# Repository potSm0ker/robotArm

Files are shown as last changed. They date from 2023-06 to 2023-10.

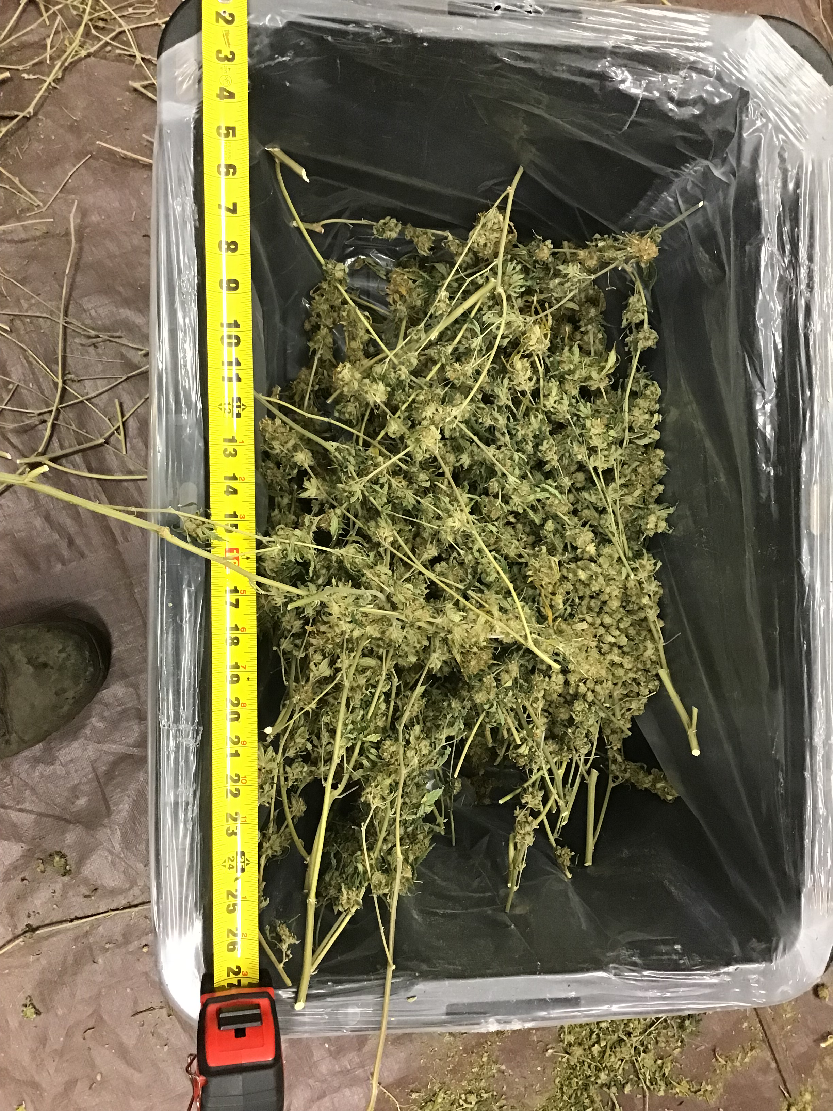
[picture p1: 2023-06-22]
workspaceExamples/binMeasured.jpg

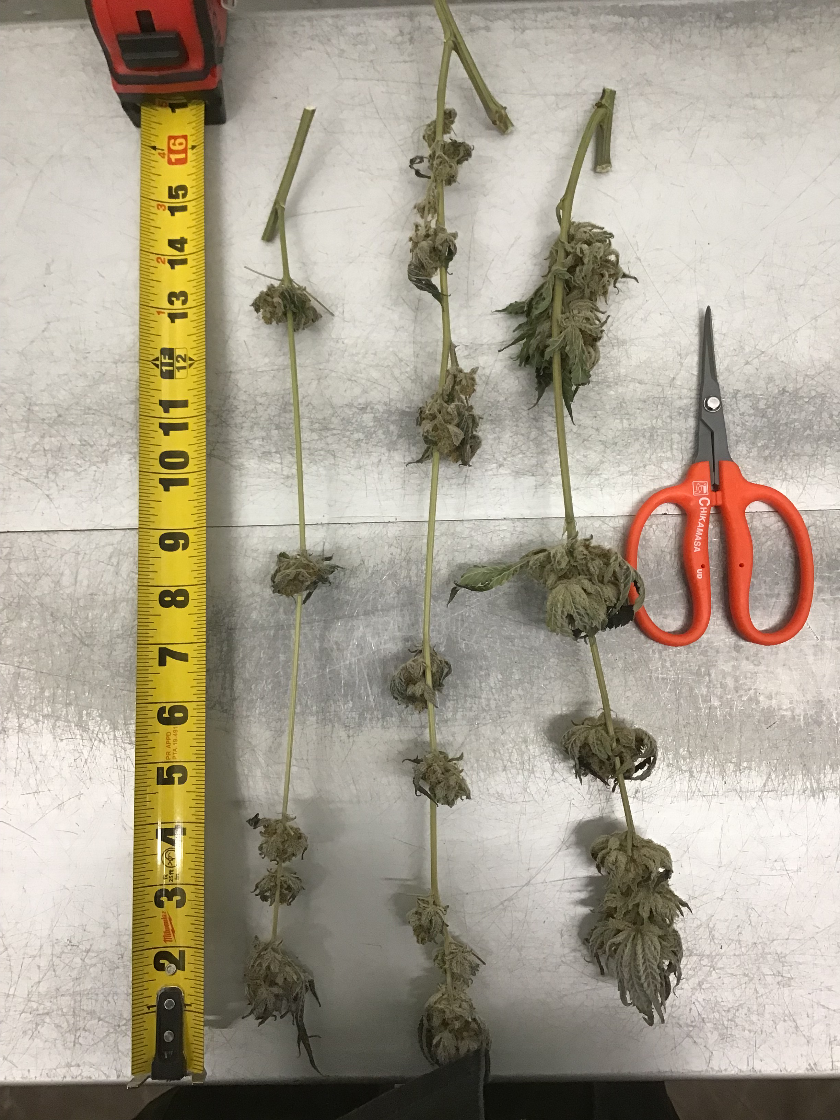
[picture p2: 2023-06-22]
workspaceExamples/branchMeasured.jpg

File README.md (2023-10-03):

# Trim Bot Project

<details>

<summary> ***30,000 foot goal.*** Create a pair of electric robot arms that can trim 1 pound of dried cannabis buds in 8 hours.  </summary>

- Create a pair of electric robotic arms that can **automatically** trim dried cannabis flowers using a standard pair of trimming scissors. **The target goal is to trim 1 pound of cannabis in 8 hours time.** The arm uses servo motors to rotate the joints. For vision- open cv or other methods of object detection using one or more cameras. The arm will be able to grasp (using a two fingered-claw) a branch or bud from a bin full of branches, then hold the branch while a second arm with standard trimming scissors attached (to the claw) will trim the buds. The finished buds will be dropped into a bucket when complete. The average human trimmer would trim for about 7.2 hours in a standard work day, 1 pound of trimmed cannabis would be the expected minimum after 8 hours. 2 pounds would be a high amount for a human trimmer in a standard 8 hour work day.
- I have a real world application for this robot. I can put it to work immediately after it is finished. I work in the cannabis industry, so I hope to have this finished before I lose my position here and have to move to a different industry. I have advanced as far as I can in the company I work for, so this is a way to advance my career without having to completely switch industries and have to start from the bottom.

<summary> ****The pair of robot arms should do the following:**** </summary>

- trim = remove all fan leaves using standard trimming [scissors](http://www.chikamasa.com/products/index.cgi?key=27) (see workspaceExamples directory) I will be using CHIKAMASA B-500SF shears(I refer to them as scissors)

- Able to grasp a branch or bud with pincer-type end effector(2 finger claw)

- Able to open and close a pair of standard trimming scissors, which will be securely attached to end effector(claw). Scissors will be detachable from claw for cleaning.

- Able to identify a single branch or bud in a bin full of similar items.

- Will need camera for object detection. 
    - using open-cv or other methods. python or c++ maybe used.
    - Yolo v5 is compatible with jetson nano.
- Able to work together as a pair of arms, one will hold the scissors(scissor arm), the other will hold a branch/bud(branch arm).

- Branch arm able to identify fan leaves on bud and coordinate with scissor arm to remove all fan leaves.

- Branch arm able to rotate the bud/branch while scissor arm opens and closes scissors to complete trim.

</details>

- I am using a RaspberryPi 4 attached to a robot arm purchased from [amazon.com](https://www.amazon.com/Yahboom-Controlled-Programmable-Robotics-Identity/dp/B09T96PS3S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)
- For a complete 3d printable robot arm, [Moveo BCN3D](https://github.com/BCN3D/BCN3D-Moveo) I may adapt the design for my uses
- Also check out this repository [Robot Arm 3d printable](https://github.com/AngelLM/Thor/tree/developer)
- I would use a 3d printing service such as www.xometry.com to print parts.
<details>

</details>

- Here is a link  to a [YouTube playlist- Build a Robot Arm](https://www.youtube.com/playlist?list=PLcbaYozXcpF65uUvdCmepFYYjx4FZ4Iwq), these videos have info that may assist in completing the goal.
I will store the info I find useful in this repository. Some code maybe generated by chat-gpt or similar methods.

### See [workspaceExamples](https://github.com/potSm0ker/robotArm/tree/main/workspaceExamples) folder for visual definition of bud, branch, fan leaf and other items.

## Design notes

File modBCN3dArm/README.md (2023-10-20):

Blender file contains modified parts, from the BNC3d robot arm Github repository.  I set it up so i could test the range of the arm and see how it interacts with working environment. 
Created with blender 3.4

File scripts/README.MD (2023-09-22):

These are scripts that I am using to control the robot and help me complete my goal of creating a pair of autonomous cannabis trimming robot arms.
Some of these scripts may only work on a raspberry pi. In the jetson nano scripts folder are scripts that were developed for jetson nano and yahboom expansion board. I started this project with the jetson nano and expansion board but switched to raspberry pi 4 because it is more user friendly and has a larger community that can provide more answers to questions.

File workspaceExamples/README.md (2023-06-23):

## This folder contains images of products the robot arm will handle and environment the robot will traverse
### The physical working environment and equipment will be described here

<details>

<summary> Definitions </summary>

### These are items that will be used in the day to day operations involving the robot.

- buds = also called flower or nugs, the final product that will be sold to consumers, the end goal
- fan leaves = attached to the buds, they will be removed with scissors and collected for processing and sale
- branches = buds are attached to the branches. The branches will be discarded after the buds are trimmed
- bin = a black plastic container used to store branches and bud. Some buds may not be attached to branches
- scissors =  standard trimming scissors will be used, available locally and normally used by human trimmers
- tray = a black plastic tray used for collecting fan leaves and trimmed buds
- bucket = a white 5 gallon plastic container that will be used to store the finished buds

</details>

## The obective is to remove the fan leaves from the buds using scissors

- Branches may be in the range of 2 inches to 24 inches length.
- Buds(flower) may be in the range of .1 inch to 3 inches in length.
- The bin dimensions are  H- 15.27 inches, W- 19.61 inches, D- 28.55 inches
- The 5 gallon bucket dimensions are H- 15 inches, D- 10 inches
- The tray dimensions are H- 5 inches, W- 18 inches, D- 10 inches
- The working space for a normal human trimmer is approximately H- 4 feet x W- 3 feet x D- 3 feet

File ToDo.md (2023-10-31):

- i want to recreate the motion of two human arms, one connected to a pair of scissors, the other holding a branch/bud while the scissor arm trims the leaves from the bud
******* 

- i obtained a 3d printer and will print a modified version of bnc3d moveo robot arm
- i will redesign the scissor arm to use a nema 17 stepper motor to open and close the scissors, this should provide sufficient torque and precision. 

- The tip of the scissor gap must have sufficient torque to cut the branch and seperate the bud from branch
- physical trim test performed with 55kg servo, leaves can be trimmed, however the tip of the scissors are not getting enough torque to cut through the branch at the branch/bud intersection.
- may need to redesign end effector
- yolov8 segmentation? combined with oak d multiple nn detections
- how to identify and return position of leaves that need to be trimmed
- range for oak d camera- Ideal range: 70cm - 8m, MinZ: ~20cm (400P, extended), ~35cm (400P OR 800P, extended), ~70cm (800P)
- i attached camera to an extension rod and steel flat bar(14 inches), it is approximately 18 in from scissors, in a fixed location behind the scissors
- for best results using spatial detection, the camera should be perpendicular with scissors, the spatial detection fails with distance of less than 11 inches  
- using custom yolov5s model and Oak D camera, i created a script that would open and close scissors when a bud is detected within 600mm(z coord) of the camera.  

https://colab.research.google.com/github/luxonis/depthai-ml-training/blob/master/colab-notebooks/YoloV5_training.ipynb

- [Make Sense AI](https://www.makesense.ai/)    -browser based, no download, no install

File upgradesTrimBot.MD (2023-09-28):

To make the robot arm (with raspberry pi 4) do what I need to do, it will need some upgrades. 

# Current parts list

### Raspberry Pi 4 with geeekpi ice tower cooling fan and servo hat
 - using [raspberry pi 4](https://www.raspberrypi.com/products/raspberry-pi-4-model-b/) for computing and to control servos
 - pwm  16 servo hat from adafruit
 - geekpi ice tower cooling fan

### Vision - Oak-D pro camera(manual focus) from [Luxonis](https://shop.luxonis.com/products/oak-d-pro)
 - detection model can run on camera, inference results will be sent to nano
 - will use yolov5 custom model to identify leaves and direct scissors to trim leaves
 - yolov5 for locating and picking branches from bin
 - created custom bracket in blender to mount camera to robot
 - custom bracket 3d printed on [Xometry.com](https://www.xometry.com/)

# August 2023 - no longer using the parts below

### Jetson nano developer kit attached to yahboom expansion board
 - started with a jetson nano, the expansion board it was attached to had no documentation that I could find, so I switched to a raspberry pi 4 with gb ram and pwm servo hat to drive the servos.

### Increase storage  SAMSUNG T7 Portable SSD 500GB
 - I used win32disk imager to write the custom jetson image provided by yahboom for the robot arm
 - running operations on the jetson nano is much faster using an external ssd via usb3 rather than a micro usb drive.
 - run  gparted    in the terminal to see partitions and expand the file system partion to use the entire 500 gb SSD, in my case it was /dev/sda1 
 - boot from usb [jetsonhacks.com](https://jetsonhacks.com/2021/03/10/jetson-nano-boot-from-usb/)
 - create backups of critical files before attempting, loss of data may occur when trying to remount file system

### Upgrade cooling fan and heat sink - GeeekPi 5V PWM Low-Profile CPU Cooler
 - I upgraded to [Ice tower cooling fan](https://www.amazon.com/GeeekPi-Low-Profile-Horizontal-Radiator-Colorful/dp/B07ZYW6ZVR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) from amazon.com

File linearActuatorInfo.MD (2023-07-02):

## info is specific to this particular project, maybe used for other projects
- Needed for this project- slide rail(linear actuator lead screw) with a length of at least, 1000mm (3 feet), to increase reach of the robotic arm
- will be mounted vertically on a wall, with robot arm attached to slide rail on a plate.
-  lead screw-driven actuators with slide rail
- nema23 stepper motor connect to jetson nano
- Digital Stepper Driver 1.0-4.5A 18-50VDC for Nema 17, 23, 24 Stepper Motor $17.88
- for connection  USB to TTL Serial Cable or FTDI Serial TTL-232 USB Cable

 - Connect the motor driver to the Jetson Nano: usb to ttl cable. The motor driver will typically use digital input pins to receive control signals from the Jetson Nano. 

- websites
 - https://openbuildspartstore.com/
 - [How to Implement a Linear Stage With Raspberry Pi](https://www.digikey.com/en/articles/easy-build-how-to-implement-linear-stage-raspberry-pi-project)

### commercially available slide rails some assembly required

- [how to assemble slide rail from open build part store](https://www.youtube.com/watch?v=56RIplHaoQs&list=PLDeI80MYQtbqZahZvCIcOPhE0wO3RirvY)
- [OpenBuilds C-Beam Linear Actuator Lead Screw 1500mm](https://openbuildspartstore.com/c-beam-tension-xl-linear-actuator-bundle/) $261.97
- [nema 23 motor + controller with usb to ttl](https://excitron.com/secure/?itemid=585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) $279.00 

- ## stepper motor drivers
- www.teknic.com
- [top choice - clear path motors](https://teknic.com/products/clearpath-brushless-dc-servo-motors/clearpath-sc/)
- [clear path motors youtube](https://www.youtube.com/watch?v=1S7etlhbuFY&list=PLuMmdjFz-3nzWAxdQWN__v9P9fYJkGCvS&index=2)
- [connect clear path motor  to arduino](https://www.youtube.com/watch?v=QZLwDnGSaeI&list=PLuMmdjFz-3nzWAxdQWN__v9P9fYJkGCvS&index=8)

 - [RTELLIGENT Nema 23 Stepper Closed Loop Servo Motor and Driver Kit 2 Phase 3.0NM(425 oz.in) with Encoder](https://www.amazon.com/RTELLIGENT-Stepper-Closed-57X57X119mm-Encoder/dp/B07ZLQL83N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)

 - [CNC Digital Microstep driver DM542 Stepper Motor Controller 2-phase Digital Stepper Motor Driver 20-50V DC Max 4.2A](https://www.amazon.com/Digital-Microstep-Stepper-Controller-2-phase/dp/B08GCFNQF2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)

 - [STEPPERONLINE 1 Axis CNC Kit 3Nm(425oz.in) Nema 23 Stepper Motor & Driver](https://www.amazon.com/STEPPERONLINE-425oz-Stepper-Driver-Router/dp/B012QFRKAO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)

## power supply
- [DROK 36V Power Supply, AC 110V 220V to DC 0-36V 4A 150W Buck Converter](https://www.amazon.com/DROK-110V-220V-Converter-Adjustable-Transformer/dp/B0B18P6GKP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)

### Found diy video and parts list

[DIY slide rail assembly youtube](https://www.youtube.com/watch?v=bwkWi0-p5mU)
- parts list for a DIY linear rail
 - Aluminium profile T-Slot 30cm
 - Aluminium profile T-Slot 5cm
 - Linear guide rail MGN12H 30cm
 - T8 2mm pitch lead screw 30cm & anti backlash nut
 - NEMA 17HS8401 stepper motor
 - NEMA 17 fixed mount bracket
 - 5-8mm flexible coupler
 - M3 Female2male brass screw thread PCB stand
 - M5 hex screw + nut + flat washer
 - M3 hex screw + nut
 - Zip ties

 [mini jetson nano car](https://medium.com/@anandmohan_8991/jetbot-using-l298n-pwm-motor-a6556ed358d6)

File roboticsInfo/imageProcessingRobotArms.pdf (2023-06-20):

See discussions, stats, and author profiles for this publication at: https://www.researchgate.net/publication/261225894
Practical applications for robotic arms using image processing (https://www.researchgate.net/publication/261225894_Practical_applications_for_robotic_arms_using_image_processing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)

Conference Paper · January 2012

CITATIONS
17

READS
9,894

### 3 authors, including:

Some of the authors of this publication are also working on these related projects:

Nonlinear Fault Tolerant Control for Real-Time Robotics View project (https://www.researchgate.net/project/Nonlinear-Fault-Tolerant-Control-for-Real-Time-Robotics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)

Intelligent control structure and navigation system based on the performance sensors, video-biometric and video-servoing sys. for complex autonomous sys. CAS-IW integrated into the technology for assisting people with severe neuro motor disabilities View project (https://www.researchgate.net/project/Intelligent-control-structure-and-navigation-system-based-on-the-performance-sensors-video-biometric-and-video-servoing-s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)

R. Solea (https://www.researchgate.net/profile/R-Solea?el=1_x_5&_esc=publicationCoverPdf)
Universitatea Dunarea de Jos Galati (https://www.researchgate.net/institution/Universitatea_Dunarea_de_Jos_Galati?el=1_x_6&_esc=publicationCoverPdf)

### 70 PUBLICATIONS 482 CITATIONS

SEE PROFILE (https://www.researchgate.net/profile/R-Solea?el=1_x_7&_esc=publicationCoverPdf)

All content following this page was uploaded by R. Solea (https://www.researchgate.net/profile/R-Solea?el=1_x_10&_esc=publicationCoverPdf) on 08 December 2014.

The user has requested enhancement of the downloaded file.

## Practical Applications for Robotic Arms Using Image Processing

Mihai Dragusu¹

, Anca Nicoleta Mihalache¹

and Razvan Solea²
, member, IEEE

Abstract— The following paper presents various applications for a robotic arm using image processing. These applications have as a basis a video camera that captures the images to be processed for either recognition and sorting or for contour coordinates extraction. Based on these captures, there were developed algorithms that enable the arm to either sort objects recognized to be having different shapes, or to draw shapes based on the coordinates received. Both the object detection and the contour coordinates extraction methods are implemented using a series of image processing techniques like border extraction, contour detection, contour extraction, along with match template and the aid of OpenCV library. Also, a PI controller that ensures the position of the robotic arm was developed.

I. INTRODUCTION
The influence and impact of digital images on modern society, science, technology and art are huge. Image processing has become such a critical component in contemporary science and technology that many tasks would not be attempted without it. It is a truly interdisciplinary subject and is used in computer vision, robotics, medical imaging, microscopy, astronomy, geology and many other fields [1] - [5].
One of the core technologies of the intelligent robot was, of course, vision, and this vision research area was called ”computer vision”, which is now regarded as a fundamental and scientific approach to investigate how artificial vision can be best achieved and what principles underlie it [6]. OpenCV (Open Source Computer Vision) is a library of programming functions for real time computer vision. OpenCV is free for both academic and commercial use. It has C++, C, Python and soon Java interfaces running on Windows, Linux, Android and Mac. The library has more then 2500 optimized algorithms [7].
OpenCV played a role in the growth of computer vision by enabling thousands of people to do more productive work in vision. With its focus on real-time vision, OpenCV helps students and professionals efficiently implement projects. The contribution of this paper is to report new practical applications for student laboratory that provide the hands-on experience that is critical for robotics education. These types of exercises supply the student with hands-on experience that complements classroom lectures and software development. Through this experience, the student confronts the hard realities of robot systems; realities such as sensor noise,

1M. Dragusu and A.N. Mihalache are students at the Faculty of Automatic Control, Computers, Electric and Electronic Engineering, “Dunarea de Jos” University of Galati, Romania dragusumihai@yahoo.com, mihalache anca@ymail.com
2R. Solea is with the Faculty of Automatic Control, Computers, Electric and Electronic Engineering, “Dunarea de Jos” University of Galati, Romania razvan.solea@ugal.ro

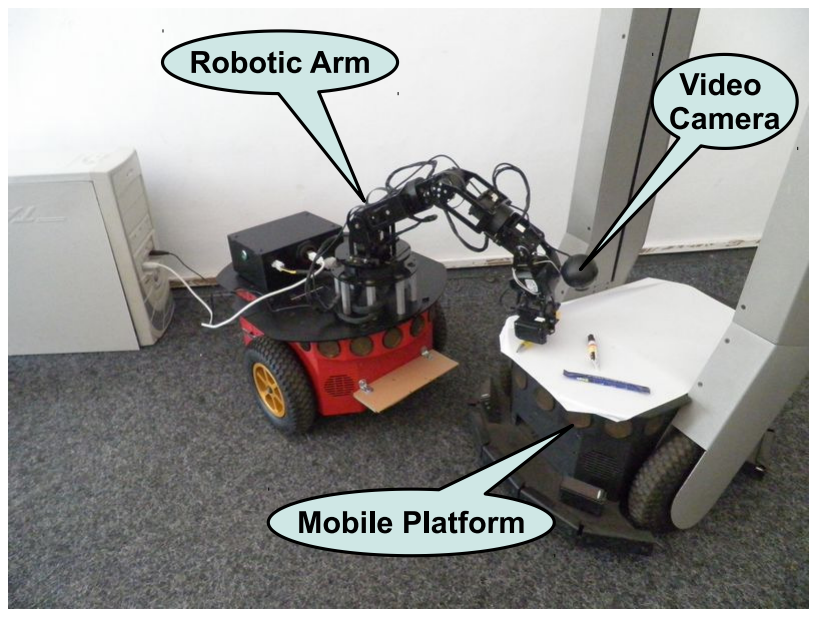
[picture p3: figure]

Fig. 1. System hardware components

nonzero calibration residuals, low fidelity of models, and real-time constraints; and learns to deal with them.
The goal of this paper is to provide an overview of the practical laboratory applications and the required facilities. As an overview, the paper will provide enough practical information to replicate the applications.

II. PRACTICAL APPLICATIONS - ALGORITHMS

The system is designed for processing images captured by a web cam so important information can be extracted and sent to the robotic arm. The robotic arm has a software implemented, so it can use the information received in order to complete its given task: either recognize shapes for sorting or coordinates extraction from a contour for drawing. System hardware components are (see Fig. 1): video camera and processing tool, robotic arm and mobile platform.

A. Contour Coordinates Extraction

The web cam captures the image to be processed. In order to obtain information about this capture, edge detection applied to the image is necessary.
Of all the edge detection techniques (Canny, Sobel, Laplace, etc.), Canny method [10], [11] was chosen because of its good performances with noisy images. This algorithm can only be applied on a grayscale blurred image, and it will find all the edges from the image, based on which contours will be formed.
After using Canny algorithm on the blurred image, it has been decided that each contour would have associated a different shade of red for each limited entity, starting from 254 and decrementing this value in successive steps with 1 until reaches the value 10. This means the detection and distinguishing of up to 244 discontinuous contours. But in

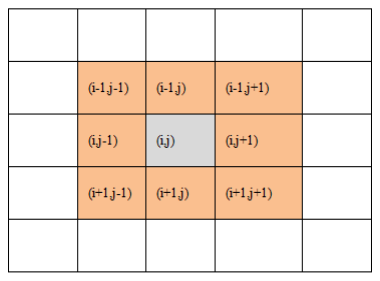
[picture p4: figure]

Fig. 2. The Moore neighborhood in coordinates

the captured image there can also exist continuous contours, that can be detected as such, and be assigned another color (blue).
These operations result in an image that contains all boundaries (edges) found in the web cam capture. These contours will have their coordinates extracted in order to be sent to the robotic arm.
It has been chosen the design of an algorithm that is optimal for the issue at hand, the drawing with the robotic arm. The image to be processed is analyzed as a matrix, and the coordinates (x, y) of a given color are saved in a matrix of unsorted coordinates.
For the drawing to be facilitated for the robotic arm, it is of the essence that the drawing of a contour does not start from a random point that first found by the algorithm, but from a start pixel of that contour (a pixel that only has one neighbor in the Moore neighborhood - see Fig. 2).
Once the start pixel is found, based on its coordinates, the sorting of addresses from the unsorted coordinate matrix will follow. This sorting is based on applying an optimization criterion that ensures finding the neighbor of the current pixel. This criterion is represented by the distance between the pixel considered current pixel, and the pixel analyzed from the unsorted addresses matrix. The sorting of the addresses is made based on this criterion, and the update of the current pixel is made by assigning the last pixel to be sorted at any point in the algorithm as the current pixel for the next iteration.
Once the address of a pixel is sorted, its coordinates are to be erased from the initial matrix, and added in the sorted coordinates matrix. This is easily followed in the following code:

if (dist < min_dist) //if current distance is lower that the minimum distance {
min_dist=dist; | //current distance is
| minimum distance
poz_adr=i;
adr_ord[linie][0]=adr1[i][0]; adr_ord[linie][1]=adr1[i][1]; }
else
{
if(dist==min_dist)
{

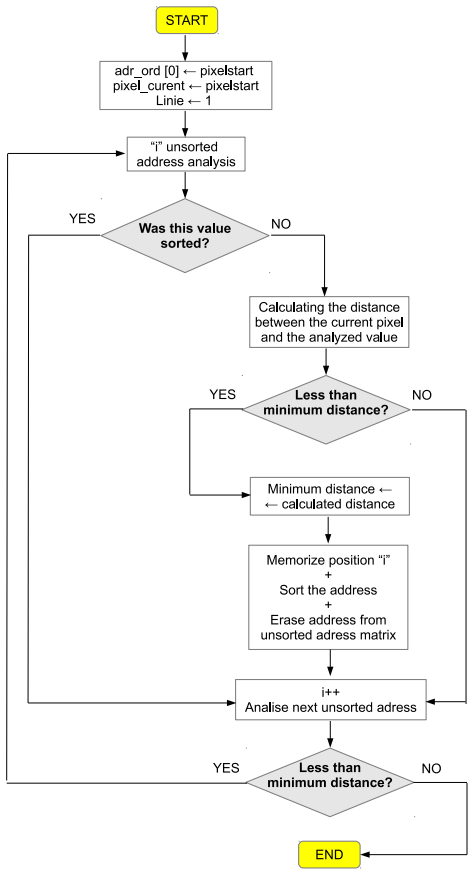
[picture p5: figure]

Fig. 3. The sorting algorithm

adr_ord[linie][0]=adr1[i][0]; adr_ord[linie][1]=adr1[i][1]; }
}
adr1[poz_adr][0]=-1;
adr1[poz_adr][1]=-1;
pixel_curent[0]=adr_ord[linie][0]; pixel_curent[1]=adr_ord[linie][1]; linie++;

The sorting of contour coordinates algorithm is presented in Fig. 3.
This implementation prevents the double passing on the same contour/region. So with this solution, no coordinate once sorted would be ever checked again. This is a very important aspect, considering the task given, because drawing the same piece of contour several time is not only useless for the arm, but also it can also emphasis the hardware limitations of the system-drawing the same piece of contour will not overlap on several drawings, even if the given coordinates are the same ones. This event occurs because of the hardware parts involved, like the arm′
s encoders.
B. Robotic Arm Software for Sorting Algorithm
In order to obtain information about the presented object, edge detection applied to the image is necessary. For the

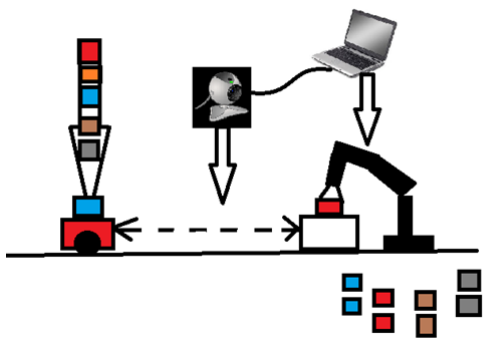
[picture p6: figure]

Fig. 4. Object recognition and sorting solution

same reason, Canny method was again chosen. After the edges are extracted from an image a contour (chain of neighbor pixels) finding method can be applied. Some contours may contain the object, since the edge of one object is a chain of pixels.
The actual recognition is realized with match-template method, which consist in placing a frame containing the object on top of the current image, calculating the sum squared error and then moving the object through the image in order to determine where the sum squared error is minimal.
It can be easily observed that the method above can prove inefficient if the number of objects to be found increases, or the size of the image increases. The application will end up looking for a 50 × 50 image in a 1920 × 1080 image filled with irrelevant data except for the actual object.
So in order to increase efficiency another method was designed based on match-template. This new method will use edge detection, contour detection, and contour extraction on the current image and only then will match-template be used between the searched object and the object extracted from the current image (resized to the dimension of the searched object). This way the application will use match-template only on relevant data, not blindly on the entire image.
For object sorting algorithm (see Fig. 4), the robotic arm will go through four states:
- A initial position at which the robotic arm will go once the control application is launched. From this position the camera placed on the arm will capture the image containing the object in order to determine its category.
- A state in which the gripper is brought to the object’s level in order to grab it.
- Return to the initial position, but this time with the object grabbed (this state is an intermediate state to avoid collision with the mobile platform if the arm were to go directly to the last state)
- The last state is actually a multitude of states generated by the object’s category (each category has assigned a different location)
The object recognition and sorting algorithm is presented in Fig. 5, where: Xdorit is the position where the mobile

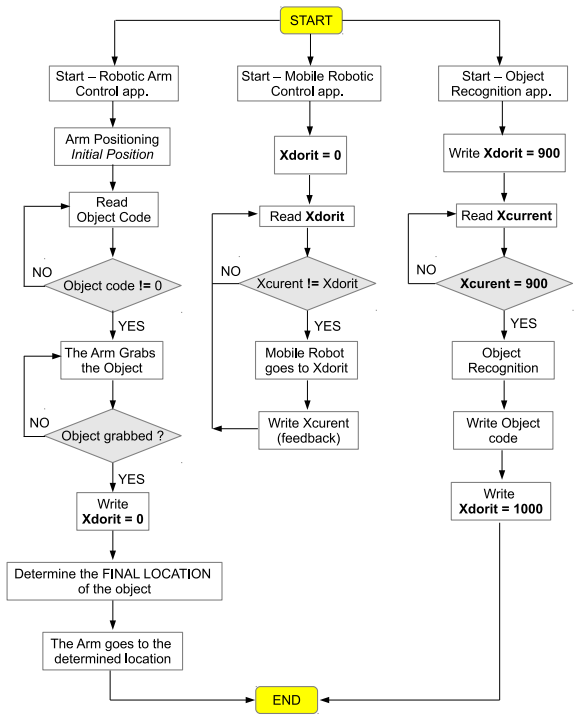
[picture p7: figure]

Fig. 5. Object recognition and sorting algorithm

Fig. 6. The control structure of robotic arm

platform should be (0 initial postion, 900 [mm] in front of the camera to determine the object, 1000 [mm] in front of the robotic arm so that it can grab the object); Xcurent is the feedback given by the platform; ObjectCode is an number which represents the detected object (the algorithm uses this number to determine the depositing position).
The control software (actinSE) [9] implemented for this robotic arm has a controller designed, but this controller does not offer the precision needed for this project so a P I controller (see Fig. 6) was designed to correct the command given by the actinSE controller.

III. FIRST PRACTICAL LABORATORY APPLICATION - EXPERIMENTAL RESULTS FOR IMAGE DRAWING

A. Step 1 - Image capture and processing

The web cam included in the system makes an image capture to be processed. Firstly it is needed to set a blur and a Canny threshold according to the image, environment and noise of the camera, with the help of this user-friendly interface, Fig. 7.

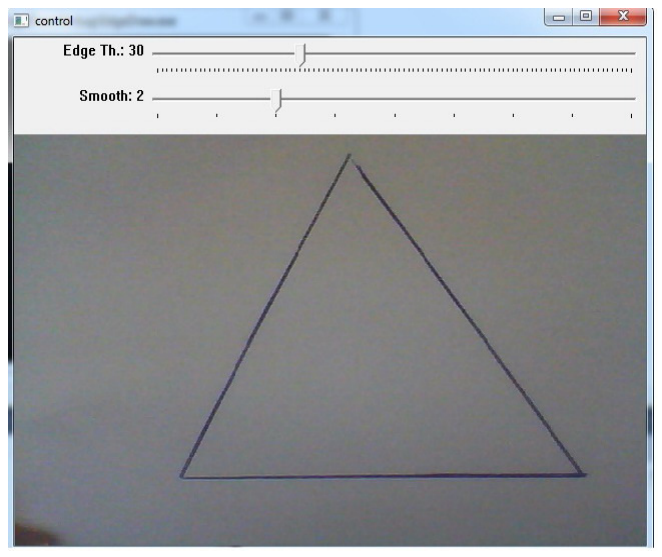
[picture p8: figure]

Fig. 7. Capture of the image to be drawn

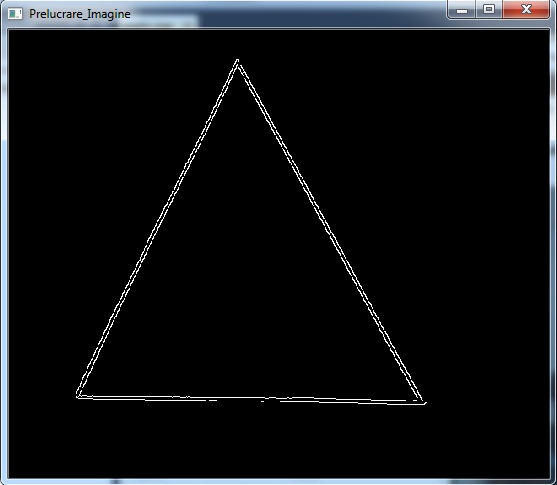
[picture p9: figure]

Fig. 8. The result of Canny algorithm on the captured image

The following code sequence is a demonstration on how the capture is prepared for Canny algorithm, by transforming it in a blurred single-channel image:

frame = cvQueryFrame( cv_cap); cvSmooth(frame,frame,CV_GAUSSIAN,smoothD,smoothD); IplImage* frgray = cvCreateImage( cvGetSize(frame), IPL_DEPTH_8U, 1 );///frame in grayscale cvCvtColor(frame, frgray, CV_RGB2GRAY );
The result of applying Canny algorithm is presented in Fig. 7, obtained with the following code sequence:

cvNamedWindow("Prelucrare_Imagine",0);
frame = cvQueryFrame( cv_cap);
cvSmooth( frame, frame,CV_GAUSSIAN,smoothD, smoothD);
cont=Canny(frame);
cvShowImage("Prelucrare_Imagine", cont);

As mentioned, these contours are to be colored in red for an easier analysis.

B. Step 2 - Robotic arm drawing coordintes
The coordinates that were extracted from this image are the Cartesian coordinates to be rescaled and translated in polar system. But for demonstration purposes, these coordinates were used for a Matlab simulation, where it was created a matrix of addresses to be plotted:

for i=1:1:s(2)
plot(a(1,i),a(2,s(2)-i));
hold on
pause(0.001);
axis([0 640 0 640]);
end

And the image that results is drawn fluently point by point for an easier observation on where the contour starts and how the contour drawing is progressing, as if the arm would be drawing. The final result of the Matlab simulation is described in the Fig. 9.
Robot arms offer significant advantages for robotic tasks. With many degrees of freedom, they are able to reach around obstacles, reconfigure for strength, improve accuracy, and manipulate objects with dexterous fluid motion.
Combined with Energid’s 3D visualization, reasoning, and control software, the Cyton V2 manipulator [8] can perform advanced control by exploiting kinematic redundancy. Cyton have 7 DOF plus gripper, all axes are completely independent yet can be controlled simultaneously (using the included Actin control software). Also, it has high performance, intelligent actuators give feedback on position, speed, load, voltage, and temperature.

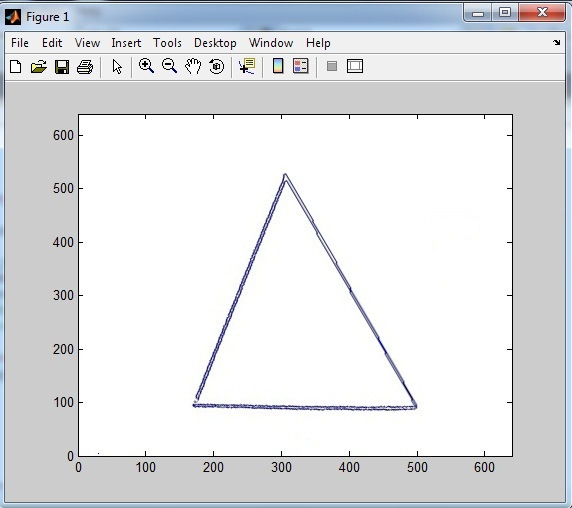
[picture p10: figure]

Fig. 9. Matlab simulation of drawing the extracted coordinates

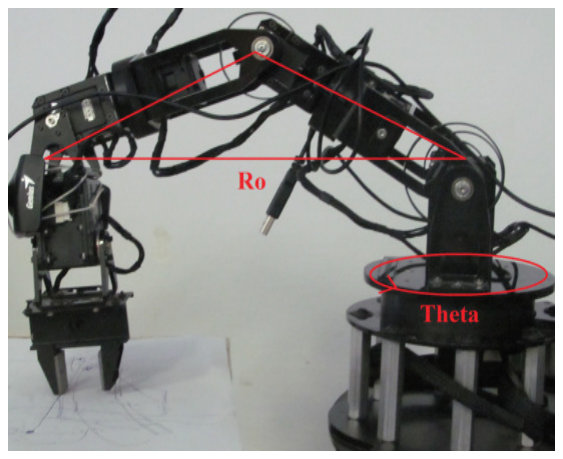
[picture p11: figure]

Fig. 10. Polar coordinates defined on the robotic arm

As for the drawing algorithm, as it was mentioned before, the coordinates provided by the contour extraction algorithm are in Cartesian system, so for the actual drawing process, they need to be converted to polar coordinate system.
The real space in which the arm can draw is limited because the distance it can reach (ρ) is not scaled correctly related to its angle (θ) (see Fig. 10. In order to solve this problem, a new scaled space had to be defined like in Fig. 11.
The polar coordinated for this space (P) were experimentally determined, and then transformed back into Cartesian coordinates (C).

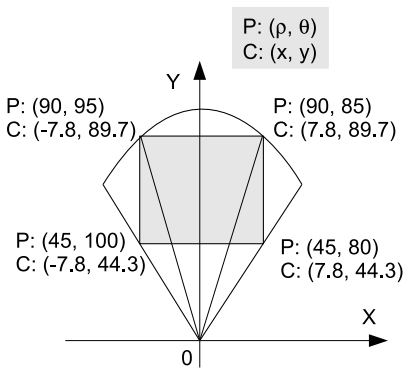
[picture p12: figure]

Fig. 11. The scaled space defined in polar coordinates

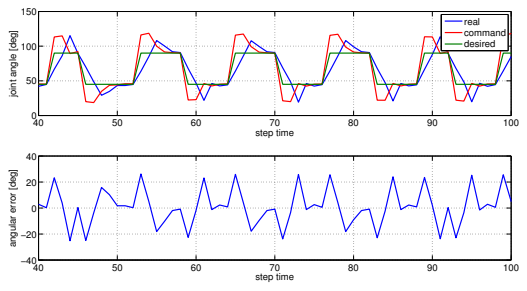
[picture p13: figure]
step time; angular error [deg]; joint angle [deg]; real command desired

Fig. 12. Joint angle variation

Knowing that the image has a width of 640 pixels and a height of 480 pixels, and based on the C coordinates calculated, two constants, one for each axis, needed to be determined, so that the coordinates extracted from the image can be scaled to this newly defined space:
- x axis rescale K1 = 15.6/640 = 0.024, where 15.6 = 2 ∗ 7.8 the distance between −7.8 and 7.8;
- y axis rescale: K2 = 45.4/480 = 0.094, where 45.4 = 89.7−44.3, roughly the distance between 89.7 and 44.3. Once these constants have been defined, the rescale formula for the Cartesian coordinates is:

xr = x ∗ K1 − 7.8
yr = y ∗ K2 + 44.3

(1)

where xr | and yr | are the rescaled coordinates and x, y are
the initial coordinates provided by the extraction algorithm. So after rescaling the drawing space and the coordinates received from the extraction algorithm and transformed into polar coordinate system, the arm can now draw the shapes presented to the camera, with a low degree of difficulty, considering the limitations it has.
Fig. 12 shows the desired, command and real angular position of the first joint of the manipulator and the angular error.

IV. SECOND PRACTICAL LABORATORY APPLICATION - EXPERIMENTAL RESULTS FOR SORTING ALGORITHM
A. Step 1 - Learning Process (object extraction)
During this process the user will help the application learn which objects to detect, using the following steps: i) the image is captured (Fig. 13 and the edge detection is applied (“c” button); ii) the contours are determined (“d” button); iii) the objects captured by the contours are browsed (“n” button) until the user finds the desired object (see Fig. 15) and saves it (“s” button).
B. Step 2 - Recognition principle
During this process (see the diagram: Fig. 17) the camera feedback is constantly checked to see the same object extraction is applied for each frame only now for each object extracted match template is applied for each object saved. When the sum squared error between two objects is less than

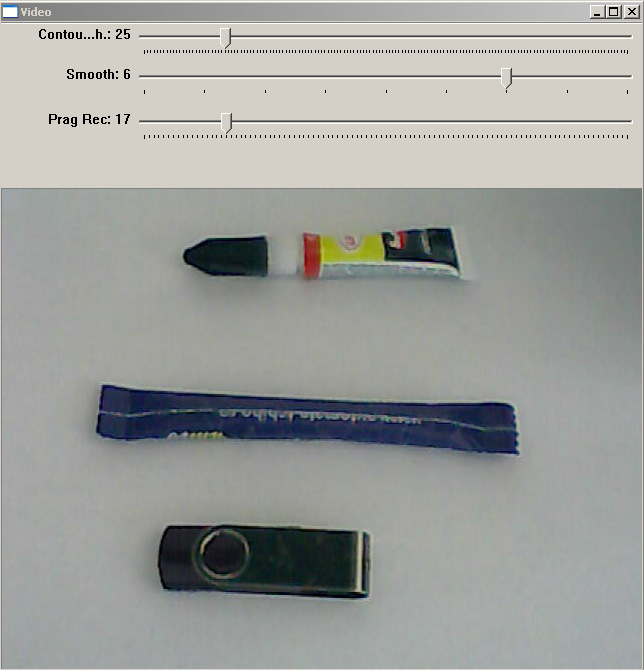
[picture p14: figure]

Fig. 13. Captured image

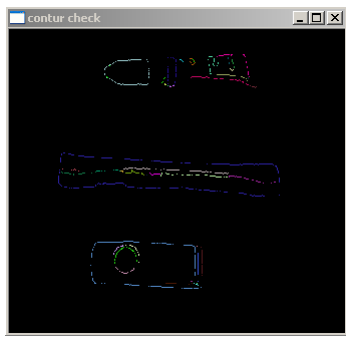
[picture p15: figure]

Fig. 14. Canny result

a predetermined threshold then we can say that the object we found (see Fig. 16 is the one were looking for.
The described process can find multiple objects in a single image.
In the following example the searched object is an USB flash stick.
In Fig. 18 the found object is declared (“stick.jpg gasit”) and its sum squared error compared to the saved one (0.0736217), as you can see other saved objects have been compared with the found object in the current image but none had the sum squared error (0.284048 and 1) low enough for a mismatch.
C. Step 3 - Object depositing

After the object has been found it’s assigned a code that is communicated to the arm’s control software which has specified places for each object type to be deposited.
To show the effectiveness of the proposed algorithm, experiments was made using a Pionner Robot mobile platform (like in Fig. 1). The mobile platform will pass through three states: i) Positioning at the input buffer coordinates; ii) Positioning under the camera in order to determine the

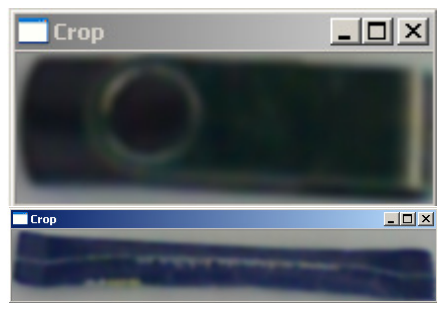
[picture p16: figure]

Fig. 15. Saved objects - example

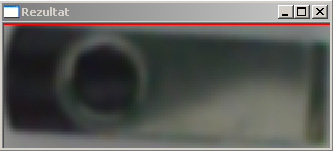
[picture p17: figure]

Fig. 16. Showing the found object

object, and to grab the object with the robotic arm; iii) Return to the initial position.
All three states are communicated (in form of Cartesian coordinates) to the mobile platform using ARIA (Advanced Robot Interface for Applications) software. The main application will write the desired position for the platform and the control application of the platform will read the file and command the robot to go to that position. ARIA software can be used to control the mobile robots like Pionner, PatrolBot, PeopleBot, Seekur etc. ARIA it is an objectoriented Applications Programming Interface (API), written in C++ and intended for the creation of intelligent high-level client-side software. ARIA provides tools to integrate I/O and includes comprehensive support for all MobileRobots robot accessories, including the laserrange finders, control of the pan-tilt-zoom camera or pantilt unit, Pioneer Gripper and Arm, and more.
V. CONCLUSIONS
In this paper it was presented practical laboratory applications in robotic manpulation, computer vision, and mechatronics. This applications provide the hands-on experience that is essential for robotics education.
The integration of real-world problems with complex imagery can improve image-processing applications. Effective applications-based exercises should be closely aligned with lecture concepts and should be assigned with little time delay. An “OpenCV” environment allows a focus on the imaging concepts and techniques with minimal programming difficulty.
Both applications, the object detection and the contour coordinates extraction methods are implemented using a series of image processing techniques like border extraction, contour detection, contour extraction, along with match template and the aid of OpenCV library.
In future work, motivated by this work, we consider the situation when mobile manipulators are sorting objects and placed the objects in a known location.

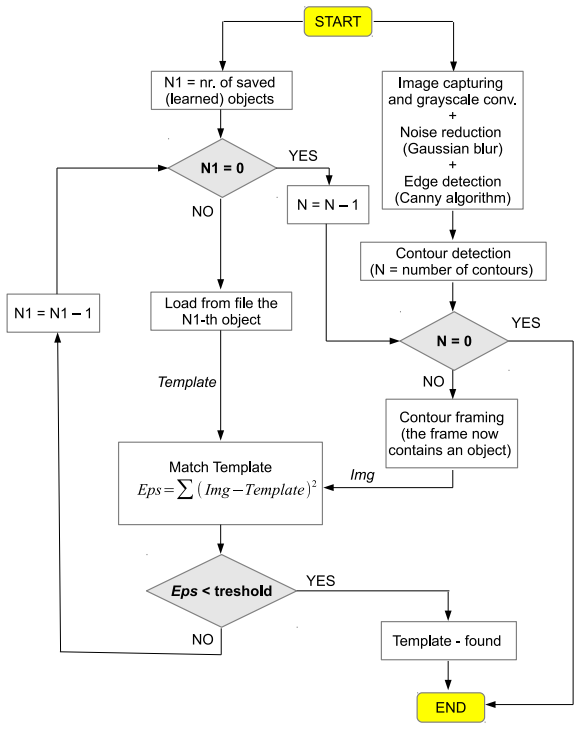
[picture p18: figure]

Fig. 17. The object recognition algorithm

Fig. 18. Result of recognition algorithm

REFERENCES

[1] C. Theis, I. Iossifidis and A. Steinhage, Image Processing Methods for Interactive Robot Control, Proceedings 10th IEEE International Workshop on Robot and Human Interactive Communication, 2001, pp. 424-429.
[2] G. Dougherty, Digital Image Processing for Medical Applications, Cambridge University Press, 2009.
[3] M. Pesenson, W. Roby and B. McCollum, Multiscale Astronomical Image Processing Based on Nonlinear Partial Differential Equations, The Astrophysical Journal, 683 (1), 2008, pp. 566-576.
[4] S. A. Drury, Image Interpretation In Geology, Nelson Thornes, UK, 2001.
[5] Yu-fai Fung, H. Lee, and M. F. Ercan, Image Processing Application in Toll Collection, IAENG International Journal of Computer Science, 32(4), 2006, 6 pages.
[6] M. Ejiri, T. Miyatake, H. Sako, A. Nagasaka and S. Nagaya, Evolution of Real-time Image Processing in Practical Applications, IAPR Workshop on Machine Vision Applications, Japan, 2000, pp. 177-186.
[7] G. Bradski and A. Kaehler Learning OpenCV (Book style), O’Reilly Media, Inc., USA, 2008.
[8] Robai, CYTON V2 7DOF - Operating Manual, USA, 2010, 36 pages.
[9] Energid Technologies, Energid ActinSE Documentation,
http: //www.robai.com/content/docs/ActinSE docs/.
[10] R. C. Gonzalez and R. E. Woods, Digital Image Processing, 3rd Edition, Prentice Hall, 2008.
[11] W. K. Pratt, Digital Image Processing: PIKS Inside, 3rd Edition, John Wiley & Sons, Inc., 2001.

View publication stats (https://www.researchgate.net/publication/261225894)

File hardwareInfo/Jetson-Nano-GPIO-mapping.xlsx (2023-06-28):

Jetson Nano J41 GPIO Expansion Header Mapping (derived from Jetson.GPIO data)
Connector Pin # | RPi Connector Label | RPi Default SoC Pull | Module connector signal name | Linux GPIO Within Chip | Assumed Linux GPIO Chip Base | Linux GPIO
1 | 3V3
2 | 5V0
3 | SDA1 | High
4 | 5V0
5 | SCL1 | High
6 | GND
7 | GPIO_GCLK | High | GPIO9 | 216 | 0 | 216
8 | TXD0 | Low
9 | GND
10 | RXD0 | Low
11 | GPIO_GEN0 | Low | UART1_RTS | 50 | 0 | 50
12 | GPIO_GEN1 | Low | I2S0_SCLK | 79 | 0 | 79
13 | GPIO_GEN2 | Low | SPI1_SCK | 14 | 0 | 14
14 | GND
15 | GPIO_GEN3 | Low | GPIO12 | 194 | 0 | 194
16 | GPIO_GEN4 | Low | SPI1_CS1 | 232 | 0 | 232
17 | 3V3 |  |  |  | 0
18 | GPIO_GEN5 | Low | SPI1_CS0 | 15 | 0 | 15
19 | SPI_MOSI | Low | SPI0_MOSI | 16 | 0 | 16
20 | GND
21 | SPIO_MISO | Low | SPI0_MISO | 17 | 0 | 17
22 | GPIO_GEN6 | Low | SPI1_MISO | 13 | 0 | 13
23 | SPI_SCLK | Low | SPI0_SCK | 18 | 0 | 18
24 | SPI_CE0_N | High | SPI0_CS0 | 19 | 0 | 19
25 | GND
26 | SPI_CE1_N | High | SPI0_CS1 | 20 | 0 | 20
27 | ID_SD
28 | ID_SC
29 | GPIO5 | High | GPIO01 | 149 | 0 | 149
30 | GND
31 | GPIO6 | High | GPIO11 | 200 | 0 | 200
32 | GPIO12 | Low | GPIO07 | 168 | 0 | 168
33 | GPIO13 | Low | GPIO13 | 38 | 0 | 38
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

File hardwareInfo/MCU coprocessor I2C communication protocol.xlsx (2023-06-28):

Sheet: 通讯协议
Function | Register | Read/Write status | Write data1 | Write data2 | Write data3 | Write data4 | Write data5 | Write data1 | Write data2 | Remark
Read version number | 0x01 | Read | 0x01 |  |  |  |  | 1-255 |  | Read the version number of the MCU(coprocessor), read data 1: version number
ontrol RGB Light | 0x02 | Write | R(0-255) | G(0-255) | B(0-255) |  |  |  |  | Control RGB color，data 1：R，data 2：G，data 3：B
Key mode | 0x03 | Write | 0-1 |  |  |  |  |  |  | Data 1: Default mode=0, K1 button is to reset the robot arm; mode=1, study mode, press K1 button to study action, RGB light will become breathing light in study mode
Main control board model register | 0x04 | Write | 01-07 |  |  |  |  |  |  | Main board：01：STC51，02：STM32，03：microbit，04：arduino，05：raspberryPi，06：jetsonNano，07：Other
Restart MCU | 0x05 | Write | 0x01 |  |  |  |  |  |  | Restart MCU
Buzzer | 0x06 | Write | 0x00-0xFF |  |  |  |  |  |  | Control the buzzer, data 1:=0: turn off the buzzer,=0xff: turn on the buzzer,=1: buzzer whistle for 0.1 second, =2: buzzer whistle for 0.2 second.... Maximum value=50, turn on the buzzer and sound for 5 seconds.
Control bus servo 1 | 0x11 | Write | 0x00-0x0F | 0x00-0xFF | 0x00-0x0F | 0x00-0xFF |  |  |  | Control a single servo, data 1: high 8-bit data of the servo position, data 2: low 8-bit data of the servo position, the two data together are the position data of the servo, the range is: 96-4000. data 3: high 8-bit data of running time high data, data 4: low 8-bit data of running time high data, the two data together are the running time, the default is 500 (500 milliseconds), and 0 means the fastest speed.
Control bus servo 2 | 0x12 | Write | 0x00-0x0F | 0x00-0xFF | 0x00-0x0F | 0x00-0xFF
Control bus servo 3 | 0x13 | Write | 0x00-0x0F | 0x00-0xFF | 0x00-0x0F | 0x00-0xFF
Control bus servo 4 | 0x14 | Write | 0x00-0x0F | 0x00-0xFF | 0x00-0x0F | 0x00-0xFF
Control bus servo 5 | 0x15 | Write | 0x00-0x0F | 0x00-0xFF | 0x00-0x0F | 0x00-0xFF
Control bus servo 6 | 0x16 | Write | 0x00-0x0F | 0x00-0xFF | 0x00-0x0F | 0x00-0xFF
Control all bus servo | 0x17 | Write | 0x00-0x0F | 0x00-0xFF | 0x00-0x0F | 0x00-0xFF |  |  |  | Control all servos at the same time, data 1: high 8-bit data of the servo position, data 2: low 8-bit data of the servo position, the two data together are the position data of the servo, the range is: 96-4000. data 3: high 8-bit data of running time high data, data 4: low 8-bit data of running time high data, the two data together are the running time, the default is 500 (500 milliseconds), and 0 means the fastest speed.
Set bus servo ID number | 0x18 | Write | 1-250 |  |  |  |  |  |  | Set the ID number of the servo. When this command is executed, all the connected bus servos will be set to the same ID number.
Control the specific servo position | 0x19 | Write | 1-250 | 0x00-0x0F | 0x00-0xFF | 0x00-0x0F | 0x00-0xFF |  |  | Control thespecific ID servo: data 1: high 8-bit data of the servo position, data 2: low 8-bit data of the servo position, the two data together are the position data of the servo, the range is: 96-4000. data 3: high 8-bit data of running time high data, data 4: low 8-bit data of running time high data, the two data together are the running time, the default is 500 (500 milliseconds), and 0 means the fastest speed.
Bus servo torque switch | 0x1A | Write | 0 and !0 |  |  |  |  |  |  | Bus servo torque switch: 0 is closed, !0 is open
Read the status of the neutral deviation setting of the bus servo | 0x1B | read | 0x01 |  |  |  |  | 0，1，2 |  | Read data 1: 0 means not set, 1 means it has been written into flash, 2 means it exceeds the adjustment range. It must be read immediately after setting the median deviation, the status will be cleared after reading or 1.5 s.
Set the median deviation of the bus servo | 0x1C | Write | 0-6 |  |  |  |  |  |  | 0: restore the default, 1-6 is the ID of the servo, it be used to set the median value of the bus servo, the default median of No.1-No.4 servo is 2000±400, the default position of No. 5 servo is 1486±300, the default position of No. 6 servois 3100 ±400 | The median value of each servo is stored in the flash fixed address, each time the angle value is sent, the median deviation value needs to be added, and then the angle data is output to the servo
Control 6 bus servos | 0x1D | Write | Write 12 data（S1_H, S1_L, S2_H, S2_L.....S6_H, S6_L） |  |  |  |  |  |  | Send the angle data of 6 servos at the same time, from S1 to S6, with the high 8 bits in the front and the low 8 bits in the back.
Control the running time of 6 bus servos | 0x1E | Write | high 8-bit | low 8-bit |  |  |  |  |  | Combine with the 0x1D register, write 0x1e first,then write 0x1d to control the running time of the servo
Run action group | 0x20 | Write | 0-2 | The high 8 bits of the servo running time | The low 8 bits of the servo running time | The high 8 bits of the action group interval time | The low 8 bits of the action group interval time |  |  | Write data 1: 0: stop motion, 1: run once, 2: run in loop
View the number of current action groups | 0x22 | read | 0x01 |  |  |  |  | 0-20 |  | Read data 1: Calculate the number of learned action
Clear action | 0x23 | Write | 0x01
Read the position of bus servo 1 | 0x31 | Write、read | 0x01 |  |  |  |  | 0x00-0x0F | 0x00-0xFF | First, write a value (0x01) to the corresponding register, add a delay (5ms). Then, read it two data, the return value is the angle data val of the servo, the high 8 bit in the front, the low 8 bits in the back. the range of val: 96~4000
Read the position of bus servo 2 | 0x32 | Write、read | 0x01 |  |  |  |  | 0x00-0x0F | 0x00-0xFF
Read the position of bus servo 3 | 0x33 | Write、read | 0x01 |  |  |  |  | 0x00-0x0F | 0x00-0xFF
Read the position of bus servo 4 | 0x34 | Write、read | 0x01 |  |  |  |  | 0x00-0x0F | 0x00-0xFF
Read the position of bus servo 5 | 0x35 | Write、read | 0x01 |  |  |  |  | 0x00-0x0F | 0x00-0xFF
Read the position of bus servo 6 | 0x36 | Write、read | 0x01 |  |  |  |  | 0x00-0x0F | 0x00-0xFF
Read the position of specific bus servo | 0x37 | read/Write | 1-250 |  |  |  |  | 0x00-0x0F | 0x00-0xFF | Read the position data of the specified ID servo, read two data, the return value is the angle data val of the servo, the high 8 bit in the front, the low 8 bits in the back. the range of val: 96~4000
Read the state of the specified servo | 0x38 | read/Write | 1-250 |  |  |  |  | 0x00,0xda,0x01 or others |  | Read the status of the designated ID servo: Data 1: Value = 0x00 means no detection or no data of the corresponding servo is read, = 0xda (218) means the state is normal, = 0x01 other abnormal states
Control PWM servo 1 | 0x51 | Write | 0~180 |  |  |  |  |  |  | Control the angle of a single PWM servo: data 1 is the angle value of the servo (0-180)
Control PWM servo 2 | 0x52 | Write | 0~180
Control PWM servo 3 | 0x53 | Write | 0~180
Control PWM servo 4 | 0x54 | Write | 0~180
Control PWM servo 5 | 0x55 | Write | 0~180
Control PWM servo 6 | 0x56 | Write | 0~180
Control PWM all servos | 0x57 | Write | 0~180 |  |  |  |  |  |  | Control the angle of all PWM servos: data 1 is the angle value of the servo (0-180)
On board key | Status | Function
K1（Default mode） | Short-press | Middle all servo
K1（Study mode） | Short-press | Save current action to flash
K1（Network configuration mode） | Long-press 5s | Raspberry Pi or jetson nano enters network configuration mode
K2 | Short-press | Close all servo torque
K2 | Long-press 10s | Open BootLoader, support to update the firmware of the MCU(coprocessor) through the serial port
K2 | Long-press 10s | Close BootLoader

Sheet: RGB灯状态指示
操作或使用情况 | RGB灯状态 | 备注
开机 | 熄灭RGB灯 | 开机初始化并熄灭RGB灯
按下按键K2 | 亮红色 | 急停功能，关闭扭矩
按下按键K1 | 熄灭RGB灯 | 打开扭矩，舵机归中
进入学习模式 | 蓝色呼吸灯 | 在学习状态为呼吸灯，每次按下K1键，呼吸灯的颜色会变化，如果出现红色的呼吸灯，则说明学习的动作组数量已满，不再学习动作，请退出学习模式，或者清除动作组后重新进入学习模式。
退出学习模式 | 熄灭RGB灯
运行动作组时 | 亮红色 | 表示无保存的动作组或者动作组数据出错
清除动作组 | 亮绿色 | 清除动作组成功
长按K2键10秒后 | 跑马灯效果 | 打开BootLoader，支持串口更新底层单片机固件
再次长按K2键10秒后 | 熄灭RGB灯 | 关闭BootLoader

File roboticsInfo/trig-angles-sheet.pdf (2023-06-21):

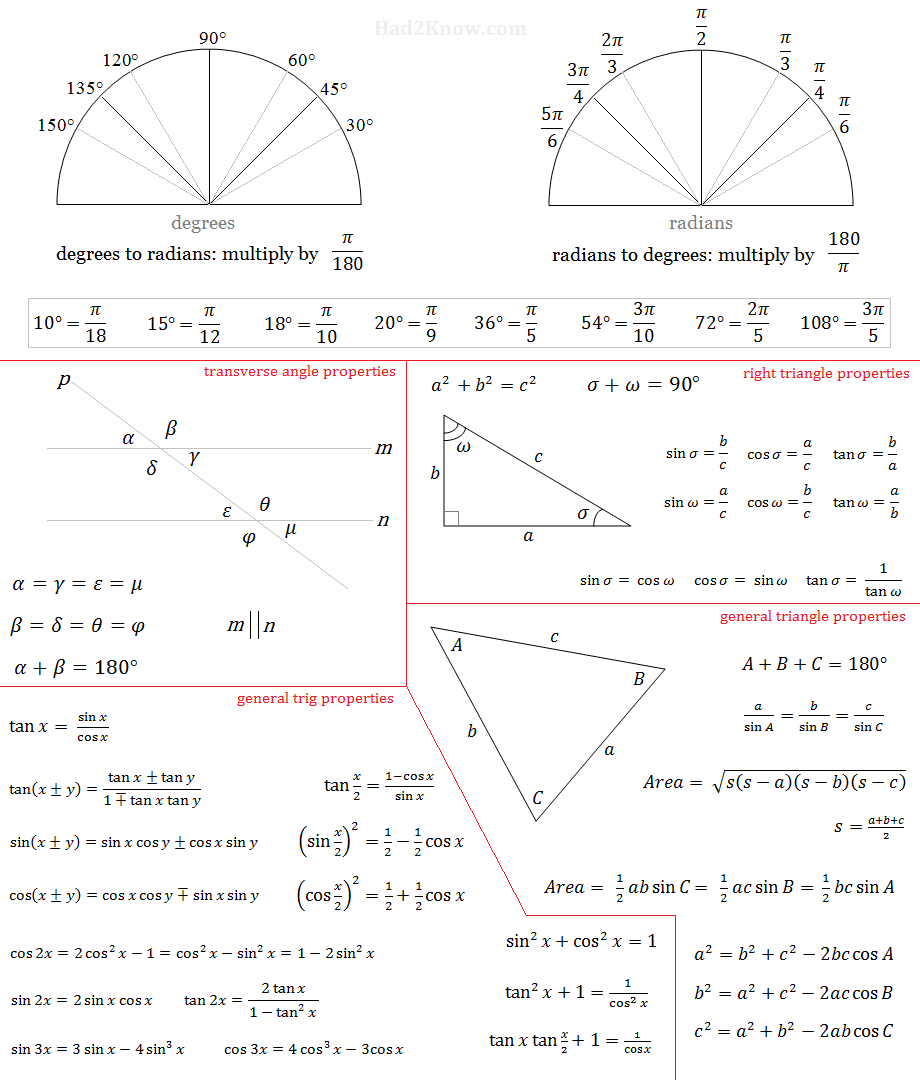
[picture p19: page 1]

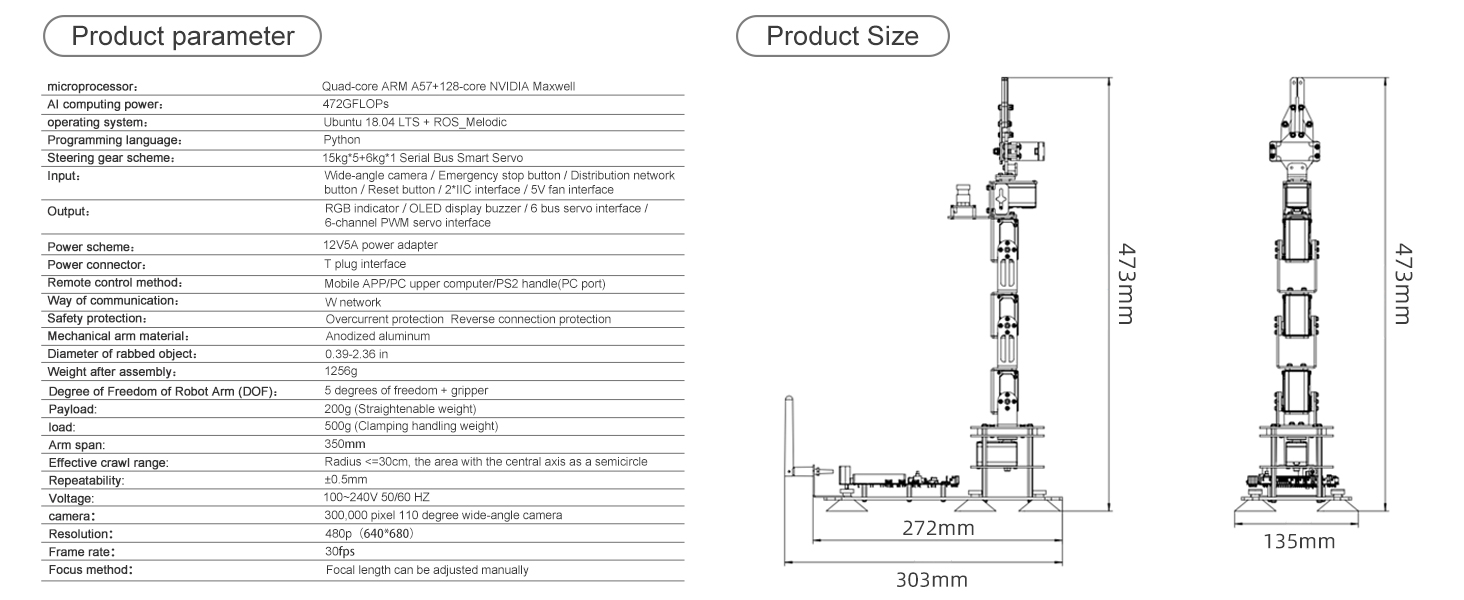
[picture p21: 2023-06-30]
hardwareInfo/armDiagram.jpg

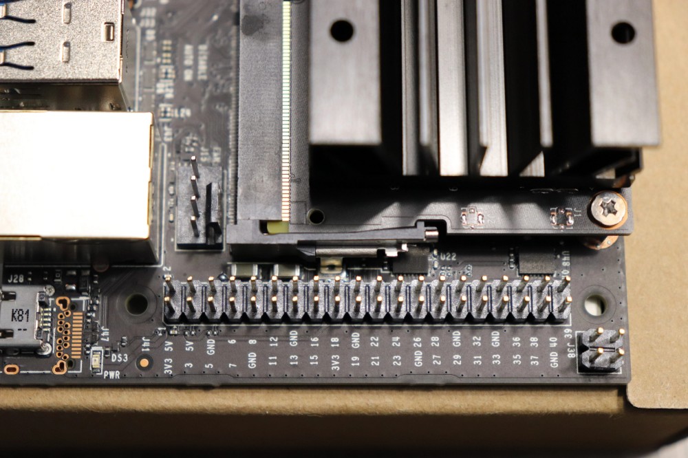
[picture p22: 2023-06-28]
hardwareInfo/jetsonNanoBoard.jpg

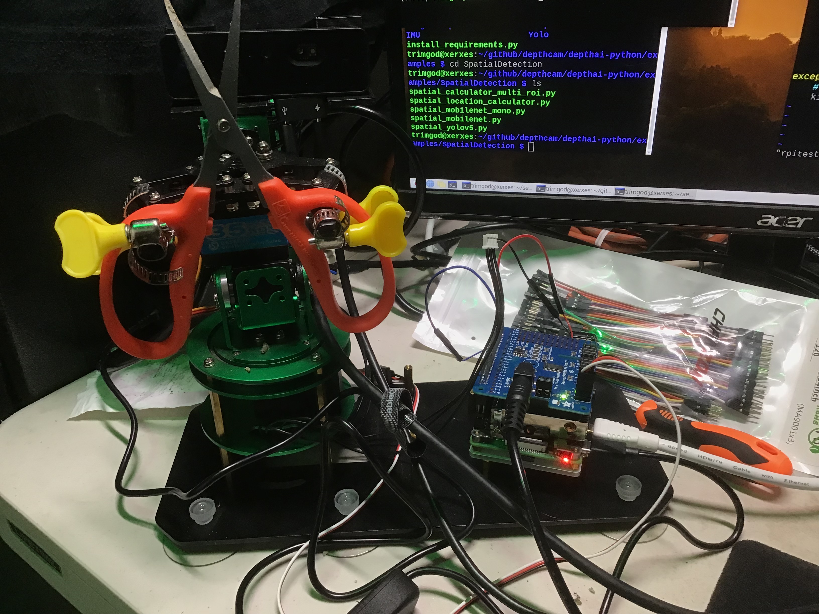
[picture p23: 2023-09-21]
currentBot.jpg

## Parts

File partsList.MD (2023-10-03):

To make the robot arm (with raspberry pi 4) do what I need to do, I will use off the shelf parts whenever possible. All parts will be mounted to a metal plate.

# Current parts list

### The base of the arm [2 DoF Pan Tilt Digital Servo Kit](https://www.amazon.com/Digital-Bracket-Building-Raspberry-unassembled/dp/B0B6PP8NFD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)
 - uses 2 pwm servos for 2 dof 
 - attached a 20kg dual output servo to give it 3 Dof
 - attached the end effector from yahboom robot arm to the 20kg servo to achieve 4 dof.

#### Raspberry Pi 4 with geeekpi ice tower cooling fan, 16 pwm servo hat and extra tall case
 - using [raspberry pi 4](https://www.raspberrypi.com/products/raspberry-pi-4-model-b/) for computing and to control servos
 - pwm  16 [servo hat](https://www.adafruit.com/product/2327) from adafruit
 - [geekpi ice tower cooling fan](https://www.amazon.com/GeeekPi-Raspberry-Low-Profile-Cooling-Heatsink/dp/B07ZV1LLWK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)
- [rpi4 case](https://www.amazon.com/ElectroCookie-Raspberry-Aluminum-Cooling-Changing/dp/B09QG349ZL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)

### digital pwm servos 55kg coreless, 35kg coreless, and 20kg(dual output)
 - I am using digital pwm servos, not serial servos. Digital servos are easier for me to control and have more precise movement. 
 - [55kg servo](https://www.amazon.com/Coreless-Steering-Aluminum-Waterproof-Shockproof/dp/B0C2Z9YX7H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)

### Vision - Oak-D pro camera(manual focus) from [Luxonis](https://shop.luxonis.com/products/oak-d-pro)
 - detection model can run on camera, inference results will be sent to nano
 - will use yolov5 custom model to identify leaves and direct scissors to trim leaves
 - yolov5 for locating and picking branches from bin
 - created custom bracket in blender to mount camera to robot
 - custom bracket 3d printed on [Xometry.com](https://www.xometry.com/)

### [Claw Grabber 2 Inch Gripping Diameter](https://www.amazon.com/USAQ-Aluminum-Controlled-Gripping-Diameter/dp/B07GDV5GRK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)
 - Aluminum Alloy, Servo Controlled - connects to servo
 - cheap aluminum 2 inch gripper

#### yahboom robot arm end effector and baseplate, stripped everything else off
 - I attached scissors to end effector and upgraded servo on bottom of end effector 
 - started with this [robot arm kit](https://www.amazon.com/Yahboom-Raspberry-Building-Programmable-Electronic/dp/B09V7H7V9Q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) 
 - from yahboom, however I could not update jetson nano, nor use the serial servos it came with. Also, the brackets for the arm only fit the servos from yahboom
 
#### [scissors CHIKAMASA B-500SF Stainless Steel](https://www.amazon.com/Chikamasa-Stainless-Scissors-Fluorine-Resin-resistant/dp/B00JSYB9I6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)

 - standard trimming scissors, cheap and effective, widely used. 
 - The shape of the handle makes it easy to attach to the end effector

**** As of August 2023 - no longer using the parts below ****

#### Jetson nano developer kit attached to yahboom expansion board
 - started with a jetson nano, it was difficult to do anything with the jetson nano. the expansion board it was attached to had no documentation that I could find, so I switched to a raspberry pi 4 with 8 gb ram and pwm servo hat to drive the servos.

#### Increase storage  SAMSUNG T7 Portable SSD 500GB
 - I used win32disk imager to write the custom jetson image provided by yahboom for the robot arm
 - running operations on the jetson nano is much faster using an external ssd via usb3 rather than a micro usb drive.
 - run  gparted    in the terminal to see partitions and expand the file system partion to use the entire 500 gb SSD, in my case it was /dev/sda1 
 - boot from usb [jetsonhacks.com](https://jetsonhacks.com/2021/03/10/jetson-nano-boot-from-usb/)
 - create backups of critical files before attempting, loss of data may occur when trying to remount file system

#### Upgrade cooling fan and heat sink - GeeekPi 5V PWM Low-Profile CPU Cooler
 - I upgraded to [Ice tower cooling fan](https://www.amazon.com/GeeekPi-Low-Profile-Horizontal-Radiator-Colorful/dp/B07ZYW6ZVR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)

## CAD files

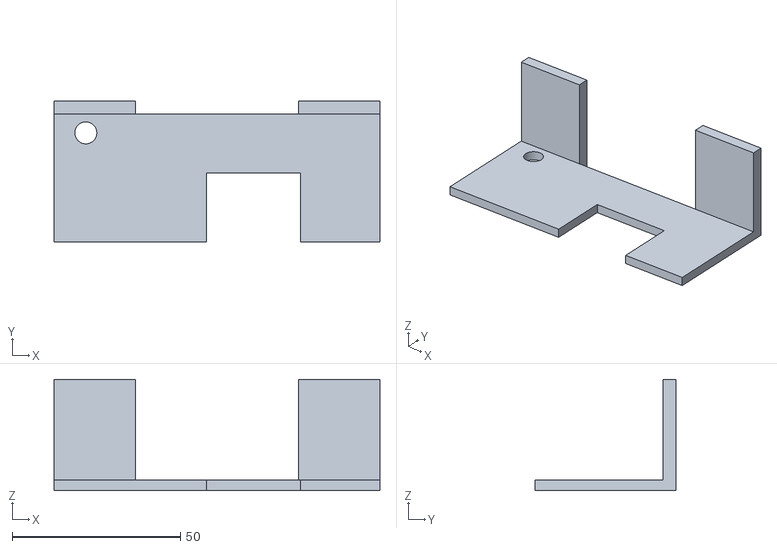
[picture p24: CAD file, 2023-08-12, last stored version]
hardwareInfo/BracketOakD.stl
97.0 x 42.1 x 33.1

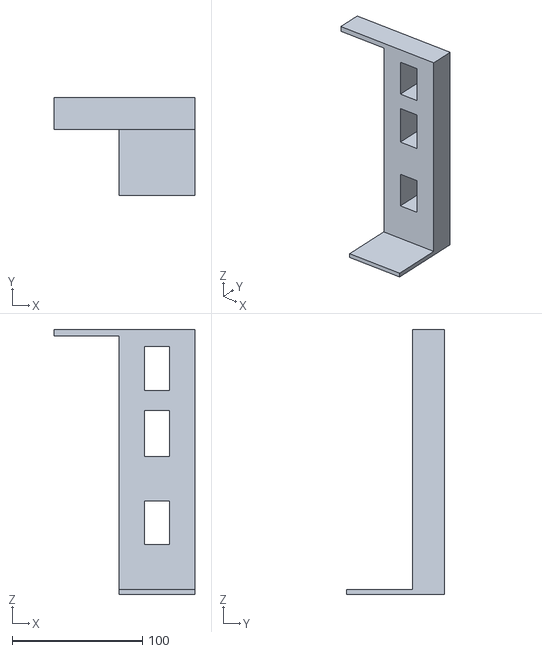
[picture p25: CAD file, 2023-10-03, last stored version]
OakD_Camera/OakDBracket_3dModel/oakdBracketV2.stl
108.2 x 75.3 x 203.8

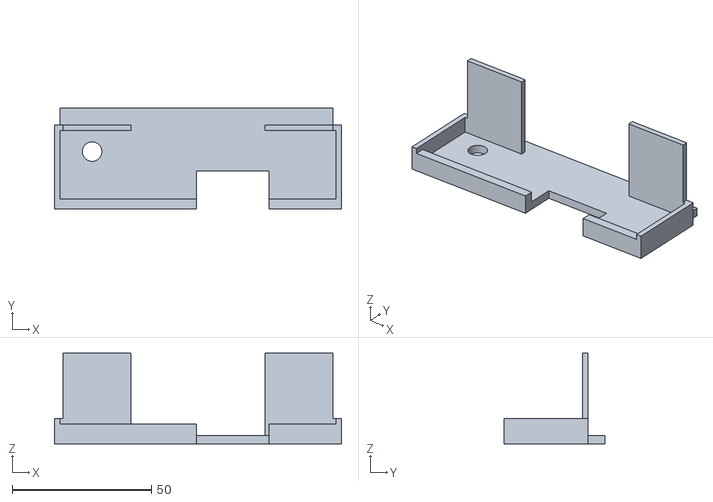
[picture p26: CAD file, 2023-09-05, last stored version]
OakD_Camera/OakDBracket_3dModel/BracketOakD.stl
103.0 x 36.1 x 32.6

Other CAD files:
OakDBracket_3dModel/BracketCamera.blend
OakD_Camera/OakDBracket_3dModel/BracketCamera.blend
OakD_Camera/OakDBracket_3dModel/oakdBracketV2.blend
hardwareInfo/BracketCamera.blend

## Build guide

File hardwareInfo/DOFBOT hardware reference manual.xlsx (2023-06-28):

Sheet: Pi&JestsonNano
 | Function | Jetson NANO physical pin | Jetson NANO BCM | Remarks
I2C interface | I2C-SDA | 3 | I2C-1 | The microcontroller (coprocessor) on the expansion board is connected to this interface, the address is 0x15
 | I2C-SCL | 5
Serial port | UART-TXD | 8 | ttyS0 | The microUSB interface is connected to this interface through the CH340 serial chip
 | UART-RXD | 10
PS2 handle receiver | PS2-MOSI | 19 | 10
 | PS2-MISO | 21 | 9
 | PS2-SCK | 23 | 11
 | PS2-CS | 26 | 7
Button K1 for wifi distribution network | WIFI-KEY | 29 | 5 | Connect KEY 1 on expansion board
Indicator light for wifi distribution network | WIFI-LED | 33 | 13
Active buzzer | Buzzer | 37 | 26
Ultrasonic interface | ECHO | 38 | 20 | Reserved external expansion interface
 | TRIG | 40 | 21

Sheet: STC51
 | Function | Pin | Remarks
I2C interface | I2C-SDA | P0.0 | The microcontroller (coprocessor) on the expansion board is connected to this interface, the address is 0x15
 | I2C-SCL | P0.1
Serial port | UART-TXD | TXD | The microUSB interface is connected to this interface through the CH340 serial chip
 | UART-RXD | RXD
PS2 handle receiver | PS2-MOSI | P1.5
 | PS2-MISO | P1.6
 | PS2-SCK | P1.7
 | PS2-CS | P1.4
Active buzzer | Buzzer | P2.0
Ultrasonic interface | ECHO | P2.2 | Reserved external expansion interface
 | TRIG | P2.1

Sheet: STM32
 | Function | Pin | Remarks
I2C interface | I2C-SDA | PB11 | The microcontroller (coprocessor) on the expansion board is connected to this interface, the address is 0x15
 | I2C-SCL | PB10
Serial port | UART-TXD | PA9 | The microUSB interface is connected to this interface through the CH340 serial chip
 | UART-RXD | PA10
PS2 handle receiver | PS2-MOSI | PB15
 | PS2-MISO | PB14
 | PS2-SCK | PB13
 | PS2-CS | PB12
Active buzzer | Buzzer | PC13
Ultrasonic interface | ECHO | PC15 | Reserved external expansion interface
 | TRIG | PC14

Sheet: Arduino UNO
 | Function | Pin | Remarks
I2C interface | I2C-SDA | SDA | The microcontroller (coprocessor) on the expansion board is connected to this interface, the address is 0x15
 | I2C-SCL | SCL
Serial port | UART-TXD | 1 | The microUSB interface is connected to this interface through the CH340 serial chip
 | UART-RXD | 0
PS2 handle receiver | PS2-MOSI | ~11
 | PS2-MISO | 12
 | PS2-SCK | 13
 | PS2-CS | ~10
Active buzzer | Buzzer | 4
Ultrasonic interface | ECHO | ~3 | Reserved external expansion interface
 | TRIG | 2

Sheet: microbit
 | Function | Pin | Remarks
I2C interface | I2C-SDA | P20 | The microcontroller (coprocessor) on the expansion board is connected to this interface, the address is 0x15
 | I2C-SCL | P19
Serial port | UART-TXD | P1 | The microUSB interface is connected to this interface through the CH340 serial chip
 | UART-RXD | P0
PS2 handle receiver | PS2-MOSI | P15
 | PS2-MISO | P14
 | PS2-SCK | P13
 | PS2-CS | P16
Active buzzer | Buzzer | P12
Ultrasonic interface | ECHO | P2 | Reserved external expansion interface
 | TRIG | P8

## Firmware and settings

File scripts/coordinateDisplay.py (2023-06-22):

import numpy as np
import cv2
#this script detects all objects in camera view and displays coordinates and bounding box
#use trackbars to adjust amount of objects detected

def nothing(x):
    pass


cv2.namedWindow("Trackbar")
cv2.createTrackbar("Threshold1", "Trackbar", 0, 255, nothing)
cv2.createTrackbar("Threshold2", "Trackbar", 0, 255, nothing)

# Set window size
window_width = 800
window_height = 600

cap = cv2.VideoCapture(0)

while True:
    ret, frame = cap.read()
    if not ret:
        break

    img_original = frame.copy()

    thresh1 = cv2.getTrackbarPos("Threshold1", "Trackbar")
    thresh2 = cv2.getTrackbarPos("Threshold2", "Trackbar")

    gray = cv2.cvtColor(frame, cv2.COLOR_BGR2GRAY)
    blurred = cv2.GaussianBlur(gray, (15, 15), 0)
    edged = cv2.Canny(blurred, thresh1, thresh2, 3)
    dilated = cv2.dilate(edged, (1, 1), iterations=2)

    contours, hierarchy = cv2.findContours(dilated.copy(), cv2.RETR_EXTERNAL, cv2.CHAIN_APPROX_NONE)

    for contour in contours:
        # Calculate the coordinates and dimensions of the bounding rectangle
        x, y, w, h = cv2.boundingRect(contour)

        # Draw a bounding box around the object
        cv2.rectangle(img_original, (x, y), (x + w, y + h), (0, 255, 0), 2)

        # Display the coordinates on the frame
        text = f'({x}, {y})'
        cv2.putText(img_original, text, (x, y - 10), cv2.FONT_HERSHEY_SIMPLEX, 0.9, (0, 255, 0), 2)

    # Resize window
    cv2.namedWindow("Output", cv2.WINDOW_NORMAL)
    cv2.resizeWindow("Output", window_width, window_height)

    cv2.imshow("Output", img_original)

    if cv2.waitKey(1) == 27:  # Press 'Esc' to exit
        break

cap.release()
cv2.destroyAllWindows()

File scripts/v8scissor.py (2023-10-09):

#!/usr/bin/env python3

from pathlib import Path
import sys
import cv2
import depthai as dai
import numpy as np
import time
import argparse
from servo import ServoController

#servo script contains functions for controlling servos
#opens and closes scissors when detection occurs
#uses yolov8 model to detect bud
#chat gpt 3.5(freeVersion) may have been involved in the development of this code


servo_controller = ServoController(servo_channel=0, min_angle=74, max_angle=178, servo_speed=2, direction=1)


''' Spatial Detection with YoloV8 example
This script will control a pair of scissors attached to a robot arm when a bud is detected within a specified range(400mm) of the camera. The scissors will open and close when the bud is detected in range.


Use tools.luxonis.com to convert your yolov5 custom model to a blob file that can be used by Oak D. Set input image shape to 416 and shaves to 5 for best results. The converter will put a few files in a zip for you to download. 
I used Oak d pro connected to raspberry pi 8gb with custom yolov5 model converted to blob to run this script.

  Performs inference on RGB camera and retrieves spatial location coordinates: x,y,z relative to the center of depth map.
  Can be used for custom yolov5 networks change nnBlobPath to your custom blob path.

I used the spatial_tiny_yolo script and modified a few lines to work with yoloV8. I made sure to change the spatialDetectionNetwork.setAnchorMasks and spatialDetectionNetwork.setAnchors to match the info in my json file obtained from blob zip downloaded from tools.luxonis.com. Lines 92 and 93
 '''

parser = argparse.ArgumentParser(description="Spatial yoloV8 example")
parser.add_argument("--model", type=str, default="nnBlobPath", help="Choose the model or provide custom path")

args = parser.parse_args()

# Get argument first
nnBlobPath = str((Path(__file__).parent / Path('models/yolov8/bud69epoch_openvino_2022.1_10shave.blob')).resolve().absolute())
if 1 < len(sys.argv):
    arg = sys.argv[1]
else:
    print("Using YoloV8 model. To use other yolos/mobilenet, use a different script")

if not Path(nnBlobPath).exists():
    import sys
    raise FileNotFoundError('The path to your blob file is incorrect, nnBlobPath')

syncNN = True

def run_scissors(distance_mm):
    
    # scissors are approx 5in(120mm)12cm from camera
    # this function will open and close the scissors when the detected leaf is within 400 mm of camera
    # the scissors and camera should be in a fixed and known position
    if distance_mm <= 900: # distance between camera and scissors
        servo_controller.move_servo()

       

# Create pipeline
pipeline = dai.Pipeline()

# Define sources and outputs
camRgb = pipeline.create(dai.node.ColorCamera)
#spatialDetectionNetwork = pipeline.create(dai.node.YoloSpatialDetectionNetwork)
#stereo = pipeline.create(dai.node.StereoDepth)
monoLeft = pipeline.create(dai.node.MonoCamera)
monoRight = pipeline.create(dai.node.MonoCamera)

nnNetworkOut = pipeline.create(dai.node.XLinkOut)

xoutRgb = pipeline.create(dai.node.XLinkOut)
xoutNN = pipeline.create(dai.node.XLinkOut)
xoutDepth = pipeline.create(dai.node.XLinkOut)

xoutRgb.setStreamName("rgb")
xoutNN.setStreamName("detections")
xoutDepth.setStreamName("depth")
nnNetworkOut.setStreamName("nnNetwork")

# Properties
camRgb.setPreviewSize(416, 416)
camRgb.setResolution(dai.ColorCameraProperties.SensorResolution.THE_1080_P)
camRgb.setInterleaved(False)
camRgb.setColorOrder(dai.ColorCameraProperties.ColorOrder.BGR)

monoLeft.setResolution(dai.MonoCameraProperties.SensorResolution.THE_400_P)
monoLeft.setCamera("left")
monoRight.setResolution(dai.MonoCameraProperties.SensorResolution.THE_400_P)
monoRight.setCamera("right")

#stereoDepth node calculates disparity and or depth from the stereo camera pair
stereo = pipeline.create(dai.node.StereoDepth)

# setting node configs changes threshold 200 for Accuracy, 245 for density
#stereo.initialConfig.setConfidenceThreshold(threshold)
#stereo.setDefaultProfilePreset(dai.node.StereoDepth.PresetMode.HIGH_DENSITY)
stereo.setDefaultProfilePreset(dai.node.StereoDepth.PresetMode.HIGH_ACCURACY)


# Align depth map to the perspective of RGB camera, on which inference is done
stereo.setDepthAlign(dai.CameraBoardSocket.CAM_A)
stereo.setOutputSize(monoLeft.getResolutionWidth(), monoLeft.getResolutionHeight())
stereo.setSubpixel(True)


spatialDetectionNetwork = pipeline.create(dai.node.YoloSpatialDetectionNetwork)

spatialDetectionNetwork.setBlobPath(nnBlobPath)

spatialDetectionNetwork.setConfidenceThreshold(0.5)

spatialDetectionNetwork.input.setBlocking(False)
spatialDetectionNetwork.setBoundingBoxScaleFactor(0.5)
spatialDetectionNetwork.setDepthLowerThreshold(100)
spatialDetectionNetwork.setDepthUpperThreshold(5000)

# yolo v5 label texts
labelMap = ["bud"]


# Yolo specific parameters
spatialDetectionNetwork.setNumClasses(1)
spatialDetectionNetwork.setCoordinateSize(4)
spatialDetectionNetwork.setAnchors([10.0, 13.0, 16.0, 30.0, 33.0, 23.0, 30.0, 61.0, 62.0, 45.0, 59.0, 119.0, 116.0, 90.0, 156.0, 198.0, 373.0, 326.0])
spatialDetectionNetwork.setAnchorMasks({ "side52": [0,1,2], "side26": [3,4,5], "side13": [6,7,8] })
spatialDetectionNetwork.setIouThreshold(0.5)

# Linking
monoLeft.out.link(stereo.left)
monoRight.out.link(stereo.right)

camRgb.preview.link(spatialDetectionNetwork.input)
if syncNN:
    spatialDetectionNetwork.passthrough.link(xoutRgb.input)
else:
    camRgb.preview.link(xoutRgb.input)

spatialDetectionNetwork.out.link(xoutNN.input)

stereo.depth.link(spatialDetectionNetwork.inputDepth)
spatialDetectionNetwork.passthroughDepth.link(xoutDepth.input)
spatialDetectionNetwork.outNetwork.link(nnNetworkOut.input)
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

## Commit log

2023-06-27 resets robot arm position to middle
2023-06-27 Create README.MD
    Individual Scripts for robot arm development
2023-06-28 Add files via upload
    hardware info
    [DOFBOT hardware reference manual.xlsx]
2023-06-30 details for pin configurations
    additional hardware can be connected directly to jetson nano to increase functionality
2023-06-30 diagram and details yahboom 6dof arm
2023-08-18 Add MountBracket_3dModel
    [BracketCamera.blend, BracketOakD.stl]
2023-08-19 Add files via git
    [BracketCamera.blend, BracketOakD.stl]
